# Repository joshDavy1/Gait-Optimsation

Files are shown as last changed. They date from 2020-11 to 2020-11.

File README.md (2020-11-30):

# Generation of Robot Gaits Using Low Level Parameters

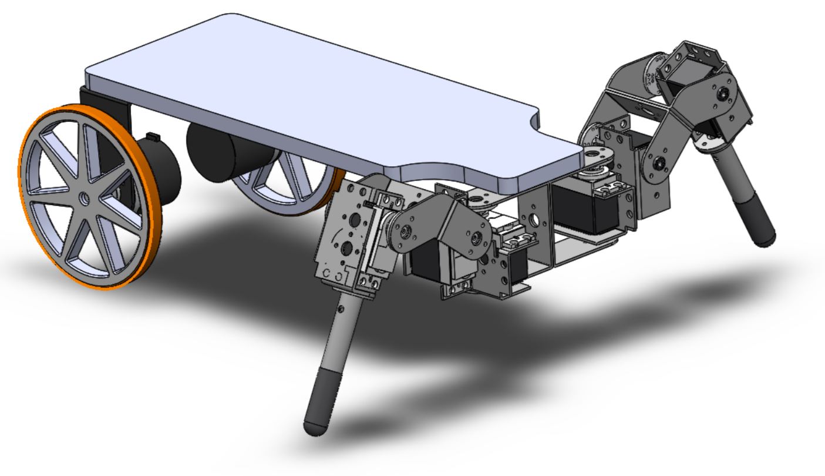
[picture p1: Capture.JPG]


Final Report

Joshua Davy

el17jd@leeds.ac.uk

May 2020

## Abstract

Traditionally the gaits of legged robots are inspired by what is seen in nature and
on assumptions of what properties the optimum gait would have. This involves
kinematic and dynamic analysis of the robot which becomes increasingly difficult
with robots with greater degrees of freedom. Further, real actuators and joints
are not ideal and are also difficult to mathematically model accurately. In this
project the aim is to use optimisation techniques to allow a robot to develop its
own gait free from human bias of what the optimum gait would look like. This
technique means no kinematic or dynamic analysis of a robot is necessary, as
the robot will attempt to learn a policy of moving its joints to optimise its gait.
The project will consist of two main sections, firstly the design and build of
a suitable robotic platform for experimentation and secondly, the investigation
and design of suitable software to control the robotic platform.

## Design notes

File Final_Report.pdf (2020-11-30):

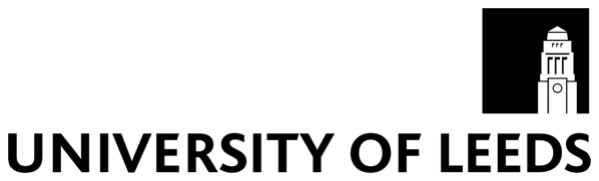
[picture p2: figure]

ELEC3875 Individual Engineering Project 2019-20

## School of Electronic and Electrical Engineering

FACULTY OF ENGINEERING

## ELEC3875

# Project Report

Generation of Robot Gaits using Low Level Parameters

Joshua Davy

SID: 2011483789 | Project No. 33
Supervisor: Dr Craig A. Evans | Assessor: Roger Berry

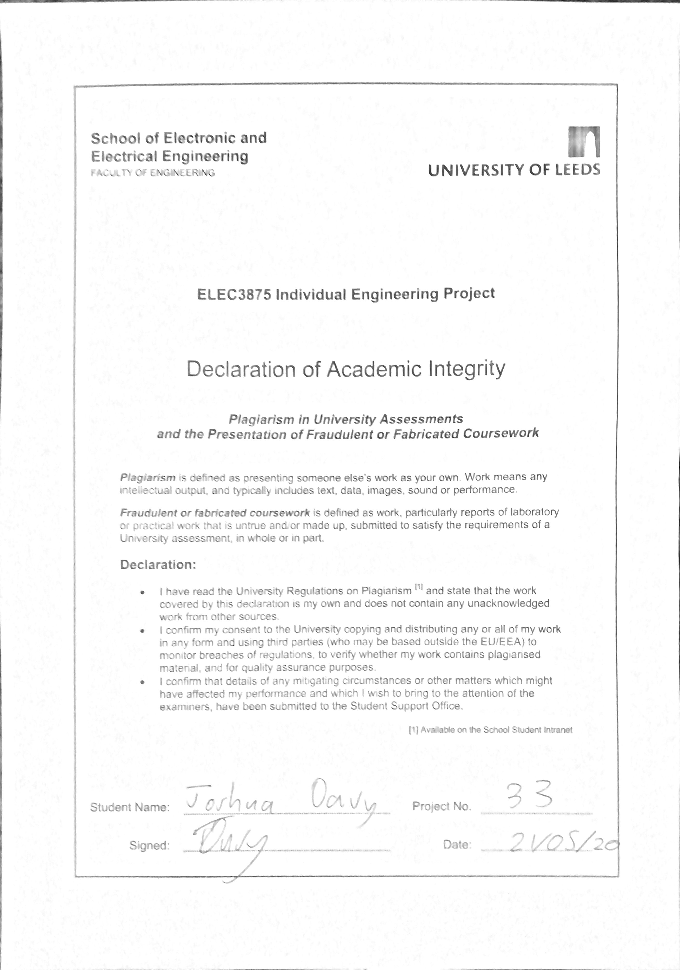
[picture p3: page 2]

# Generation of Robot Gaits Using Low Level

# Parameters

Final Report

Joshua Davy

el17jd@leeds.ac.uk

May 2020

## 1 Abstract

Traditionally the gaits of legged robots are inspired by what is seen in nature and

on assumptions of what properties the optimum gait would have. This involves

kinematic and dynamic analysis of the robot which becomes increasingly difficult

with robots with greater degrees of freedom. Further, real actuators and joints

are not ideal and are also difficult to mathematically model accurately. In this

project the aim is to use optimisation techniques to allow a robot to develop its

own gait free from human bias of what the optimum gait would look like. This

technique means no kinematic or dynamic analysis of a robot is necessary, as

the robot will attempt to learn a policy of moving its joints to optimise its gait.

The project will consist of two main sections, firstly the design and build of

a suitable robotic platform for experimentation and secondly, the investigation

and design of suitable software to control the robotic platform.

3

## 2 Acknowledgements

I would like to thank Dr Craig A. Evans for supervising this project. His help

and support have been vital to this project’s success, and his ability to help

debug and overcome countless issues I’ve faced, has saved me many painful

hours. I would also like to thank Andrew Bilbrough for his technical help. Due

to the COVID-19 outbreak, the final stages of this project had to be completed

from my family home. I would therefore like to thank my mum for her tolerance

of having robotic testing in her kitchen, the dog of which, was less understanding.

4

## Contents

1 Abstract | 3
2 Acknowledgements | 4
List of Figures | 7
List of Tables | 7
List of Algorithms | 7
3 Introduction | 8
4 2D Simulation of Gait Optimisation | 13
5 Platform Design and Build | 15
6 Platform Interface Software | 20
7 Gait Parameterisation | 21
8 Gait Optimisation Techniques | 25

5

9 Results | 29
10 Conclusion | 36
11 Future Work | 37
12 References | 38

6

## List of Figures

1 | MIT Mini Cheetah [2] | | 8
2 | The Single Legged Simulated Robot | | 13
3 | Simulation Results | | 15
4 | Final Platform CAD | | 16
5 | Revised PCB Design | | 19
6 | Human joint angles at comfortable (A) and fast (B) walking pace.
[12] | | 23
7 | Experimental Setup for Flat Surface Optimisation | | 29
8 | Comparison of Gait Parameterisations with Hill Climbing Opti-
misation | | 30
9 | Comparison of Gait Parameterisations with Genetic Optimisation 31
10 | Comparison of Gait Parameterisations with Bayesian Optimisation 32

## List of Tables

1 | Summary of Mechanical Components | | 16
2 | Summary of Changes in Revision 1.1.0 of the Robot Control Board. 18
3 | CMDMessenger [11] Commands | | 21

## List of Algorithms

1 | Stochastic Hill Climbing | | 14
2 | Stochastic Hill Climbing with Random Starts | | | 26
3 | Simple Genetic Optimisation | | 26
4 | Bayesian Optimisation | | 27

7

## 3 Introduction

### 3.1 Project Background

The recent work of groups such as Boston Dynamics and MIT is well known

with many videos featuring legged robots such as Atlas [1] and Mini Cheetah

[2] going viral on social media. Although mechanically these robots are very

capable, the crux of the problem lies in the control. Legged robotics need to

quickly react to changes, understand and process their environment, and plan

their movements accordingly.

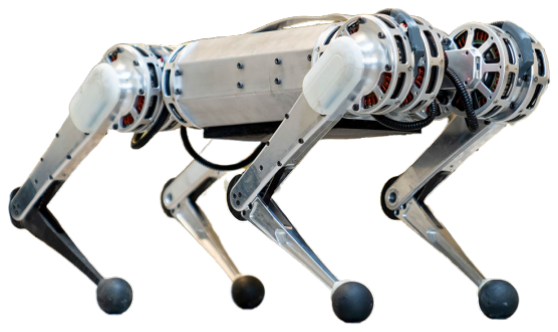
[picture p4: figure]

Figure 1: MIT Mini Cheetah [2]

To this end, often machine learning techniques are applied for the purpose

of robotic control. Learning techniques allow a robot to develop its own control

processes through experimentation with its environment. Machine learning is

the study of algorithms designed to complete an objective without being given

explicit instructions on how to do so. A machine learning algorithm aims to

complete its objective instead by forming patterns found by training [3]. In this

project, the focus is on gait generation for a legged robot. Traditionally the

gaits of legged robots are inspired by what is seen in nature and on assump-

tions of what properties the optimum gait would have. More recently, machine

learning techniques are being applied to the generation of gaits to overcome the

8

issue of designing and optimising a gait by hand. These machine learning tech-

niques require large amounts of test data in order to produce good results and

therefore often rely on simulations where the collection of data is fast and re-

quires no human intervention. The issue of simulations is they require accurate

mathematical models of the robot and its environment which are not always

attainable. In fact, it is impossible for any simulation to perfectly model the

circumstances a robot will face in reality, and a robot whose gait performs well

in simulation may perform poorly in the real world. This issue known as the

reality gap is an active part of robotics research [4]. Several solutions exist such

as Automatic Domain Randomisation [5] or Intelligent Trial and Error (IT&E)

[6].

Of course, these issues could be avoided entirely if instead of simulation, real

robots were used for the evaluation of gaits. This comes with several disad-

vantages. Firstly, the speed it takes to evaluate the gait. In simulation, gait

evaluation can take place as fast as the computer is able to process it allowing

thousands of evaluations in the time it would take a real robot to complete one.

Further, multiple simulations can run in parallel allowing faster evaluation. Al-

though multiple real robots can be used this comes at significant financial cost.

Secondly, in a simulation it may be perfectly reset, whereas in reality this is

impossible meaning no two real gait evaluations will be under the same condi-

tions. Identical gaits tested multiple times may perform drastically differently

in the real world. For these reasons, the optimisation of gaits for state of the

art legged robots rely on simulations for training or a mixture of simulation and

real world testing (Sim-to-Real [7]).

This project considers the problem of gait generation under the following con-

straints:

- No simulation of the robot and it’s environment. All gait evaluations will

need to use the real robot.

9

- No kinematic or dynamic analysis of the robot will be first derived so low

level parameters of the gait will be used. This means, for example, instead

of commanding the position of the foot of the robot, the raw control signals

to the robot motors will be used.

With these constraints the robot platform design is independent from the

gait control meaning the robot’s physical properties or environment could change

and the gait generation process would still be suitable.

As discussed above, these constraints mean the generation of gaits for a mod-

ern dynamic robot in the real world would be infeasible as the training process

would take a impractical amount of time. Therefore, for this project the scope

is limited as follows:

- The used robot platform will be statically stable. This will mean that the

robot is never in a position where another state is unfeasible to move to.

Further, the training process will require less human intervention as the

robot cannot topple.

- The gait control will sensor less and the environment constant (single

state). This means the robot is not expected to make specific plans for

obstacles or path plan. That is not to say that a gait that can deal with

obstacles will not be more advantageous. The gait will therefore be a

constant cyclic pattern, the properties of which will be generated.

### 3.2 Problem Definition

In this approach, the problem of gait generation is framed as an optimisation

problem

π

∗ = argmax

π

f(h(g(π))).

π is the policy, a vector of values that define the current gait. g is the gait

parameterisation; this maps the the policy to the cyclic sequence of control

10 values which form the gait. h is the evaluation function, the testing of a gait

on the real robot. Due to the evaluation taking place on the real robot, h is

slow to evaluate and likely to be noisy due to uncontrollable disturbances. f

is the fitness function. This maps the gait evaluation to a fitness value. The

higher the value of the fitness function will correspond to a better performing

gait. π

∗
is the global maximum. The theoretical policy with the highest fitness

and therefore the best performing policy.

The project has therefore been broken down as follows:

- Firstly, the design and testing of a 2D simulation of a simplified robot as

a initial experiment to test the theory and aim to guide the approach for

the real robot.

- The design and build of a suitable robotic platform complete with elec-

tronics and wireless interface software.

- The design of several gait parameterisation methods. This will allow com-

parison between methods.

- The investigation of suitable optimisation methods.
- The comparison of these optimisation processes with different methods of

gait parameterisations in various scenarios.

In semester one, the focus was on initial design for the robotic platform,

the 2D simulation, sourcing parts, and producing a PCB to host the control

electronics. Due to unexpectedly long lead times on certain key components,

assembly of the platform was pushed to the start of the second semester.

### 3.3 Key Terms

Gait - The pattern of steps a robot makes to walk.

Forward Kinematics - The calculation of the position of the foot of the robot

leg from its joint angles.

11

Inverse Kinematics - The calculation of the joint angles of the robot leg

from a desired foot position.

Parameter - A single parameter describes one property of the robot’s gait.

Policy - The set of parameters that fully describe the robot’s gait. The policy

has a size of n.

Gait Parameterisation - The function that maps the policy to the sequence

of joint positions that form the gait.

Fitness - The resulting score of testing the gait on the real robot. A higher

score corresponds to a better gait.

Parameter Space - The n dimensional space of possible parameter values

mapping to the corresponding fitness. The goal of any of the machine learning

algorithms is to explore this parameter space in search of the maxima.

Local Maxima - A policy in the parameter space which has a higher fitness

then the surrounding points.

Global Maxima - The policy with the highest fitness in the parameter space.

The goal of optimisation is to find this global maxima.

12

## 4 2D Simulation of Gait Optimisation

### 4.1 Simulation Design

A simple 2D simulation of a robot with a singular leg (A crawler robot) was

created in order to test the theory and experiment in simulation.

The code is written in Python and makes use of Pymunk [8] a Python wrapper

for the Chipmunk physics simulation software. The gait was parametrised as

5 sets of pairs of joint angles (for each of the two joints in the leg). The gait

is then formed by cycling through the pairs of joint angles. The policy is then

evaluated by cycling through it on the simulated robot five times and the fitness

is the distance travelled. Optimisation is performed by stochastic hill climbing

where each generation is formed by random variations of the last [9]. Variations

of the policy are formed by varying each parameter with a Gaussian distribution

N (θi
, 0.1) where θi
is the current parameter value. The below link is a video

demonstrating the simulation:

https://youtu.be/vynnbg6c0SE

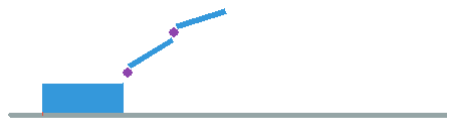
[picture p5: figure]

Figure 2: The Single Legged Simulated Robot

13

Algorithm 1: Stochastic Hill Climbing

currentP olicy ← randomInitialP olicy();

while !done do

polices ← create10RandomV ariations(currentP olicy);

evaluate(polices);

currentP olicy ← getHighestScoring(polices);

end

### 4.2 Results

Results were discussed in depth in the interim report. The main conclusions

of the simulation were despite the simplicity of the optimisation process the

formation of well performing gaits was possible in low number of evaluations.

Due to the inherit randomness of the algorithm, runs could be radically different

in results. With some runs, the algorithm could converge to a policy with a

fitness of over 1000, some runs could not get past 300. This clearly illustrates

the local maxima problem of optimisation where the algorithm gets stuck at a

maxima and cannot improve its policy from there. In Figure 3 we see a typical

run of the simulation. At first the robot makes little progress in forming a gait

until around the 5th generation where there is a radical increase in policy fitness.

After generation 50 the gait no longer makes any meaningful increase in fitness.

This shows the algorithm is stuck at a local maxima as we know better policies

do exist yet the algorithm can longer improve.

14

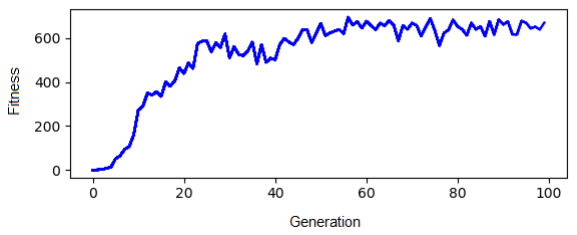
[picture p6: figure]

Figure 3: Simulation Results

## 5 Platform Design and Build

The physical robot needs to be specifically designed in order to suit the gait

training process. Mainly there needs to be a way of accurately measuring ve-

locity feedback from the robot. The system also must be stable in any position

it may find itself in. This is due to the extensive training process the robot will

have to on go to optimise it’s gait. In [9], training was in the order of hours

therefore the robot needs to be able to continue training with minimum human

intervention.

### 5.1 Assembly

The designed platform has two 3-DOF legs at the front with wheels with mounted

encoders at the rear. The purpose of the wheels is to keep the platform stat-

ically stable and prevent the robot toppling. The encoders mounted to the

wheels provide the feedback to the system allowing the measurement of the

robot’s distance travelled, velocity and acceleration. Initially all servos were

Hitec HS-422, however in initial testing the robot did not have the torque to lift

it self off the ground on one leg. The ’knee’ joints of the robot (joint two) were

replaced with high torque Hitec HS-645MG servos to compensate for this issue.

15

A small caster wheel was added to the front of the robot to improve stability

(not shown in CAD). In experimentation the effect of this caster wheel will be

tested.

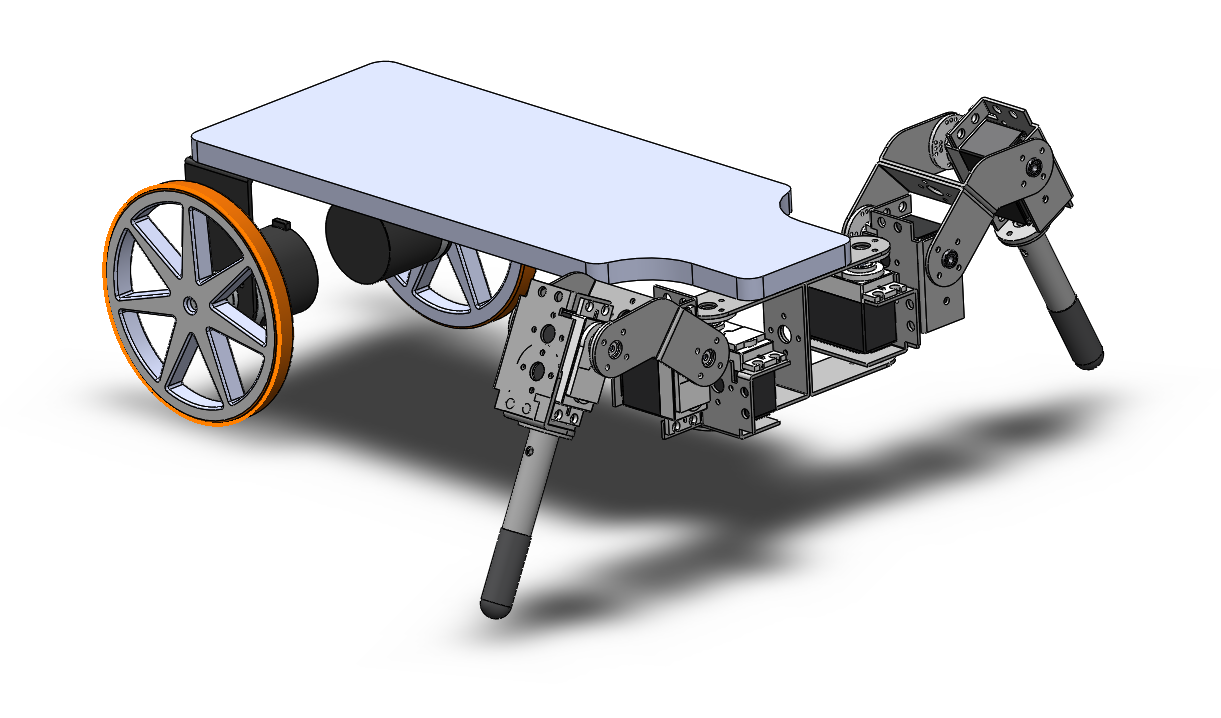
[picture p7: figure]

Figure 4: Final Platform CAD

Component | Description
Lynxmotion 3DOF T-Hex Leg Kit Pair | Robot Legs.
4 x Hitec HS-422 Servos | Servos for joints one and three in each leg.
2 x Hitec HS-645MG | Servos for joint two in each leg.
2 x Aluminum Long ”C” Servo Bracket | Brackets for connecting to robot legs to base.
Robot Base | Laser cut 8mm acrylic robot base.
2 x 400P/R encoders with mount-ing brackets. | Encoders for mounting wheels.
2x 106mm aluminium wheels with rubber coating. | Wheels for rear of the robot. High friction.

Table 1: Summary of Mechanical Components

16

### 5.2 Robot Control Board

For control of the robot a custom PCB was designed to host the main circuitry of

the robot. The board contains a ESP32 [10] microcontroller which was selected

for its WiFi and Bluetooth capabilities, as well as it’s low power consumption

and high processing power. The board contains mounting point for a inertial

measurement unit, a few buttons and LEDs for general use, ten servo mounts

as well as encoder connections. The Robot Control Board was designed to be

a general control board for servo based robot projects. This, along with the

interface software to be open sourced for others to use.

The initial PCB design (Revision 1.0.0) had several small oversights. Once

the design had been fully tested and all issues had been found, a second revision

with several new components and key changes were added (Revision 1.1.0).

Below lists the issues faced with Revision 1.0.0 and the changes made in Revision

1.1.0.

17

Issue | Fix
Servo and encoder pins were mis-labelled on silkscreen. | Silkscreen text was changed to the correct pin names.
Encoder 1 header orientation was opposite to encoder 2. | Encoder 1 header orientation flipped.
Encoder 1B pull up resistor con-nected to Pin 12 of ESP32 causes the processor to fail to boot. | Switched to internal pull up resistors for the encoders.
Pins used for tactile buttons do not have internal pull ups. | External pull up resistors added.
Servos cut out due to lack of cur-rent. | Two 10mF capacitors added to smooth volt-age. Separated microcontroller and servo power rails. Screw terminals added.
IMU used is hard to source and rel-atively expensive. | Switched to a more common and cheaper IMU.

Table 2: Summary of Changes in Revision 1.1.0 of the Robot Control Board.

18

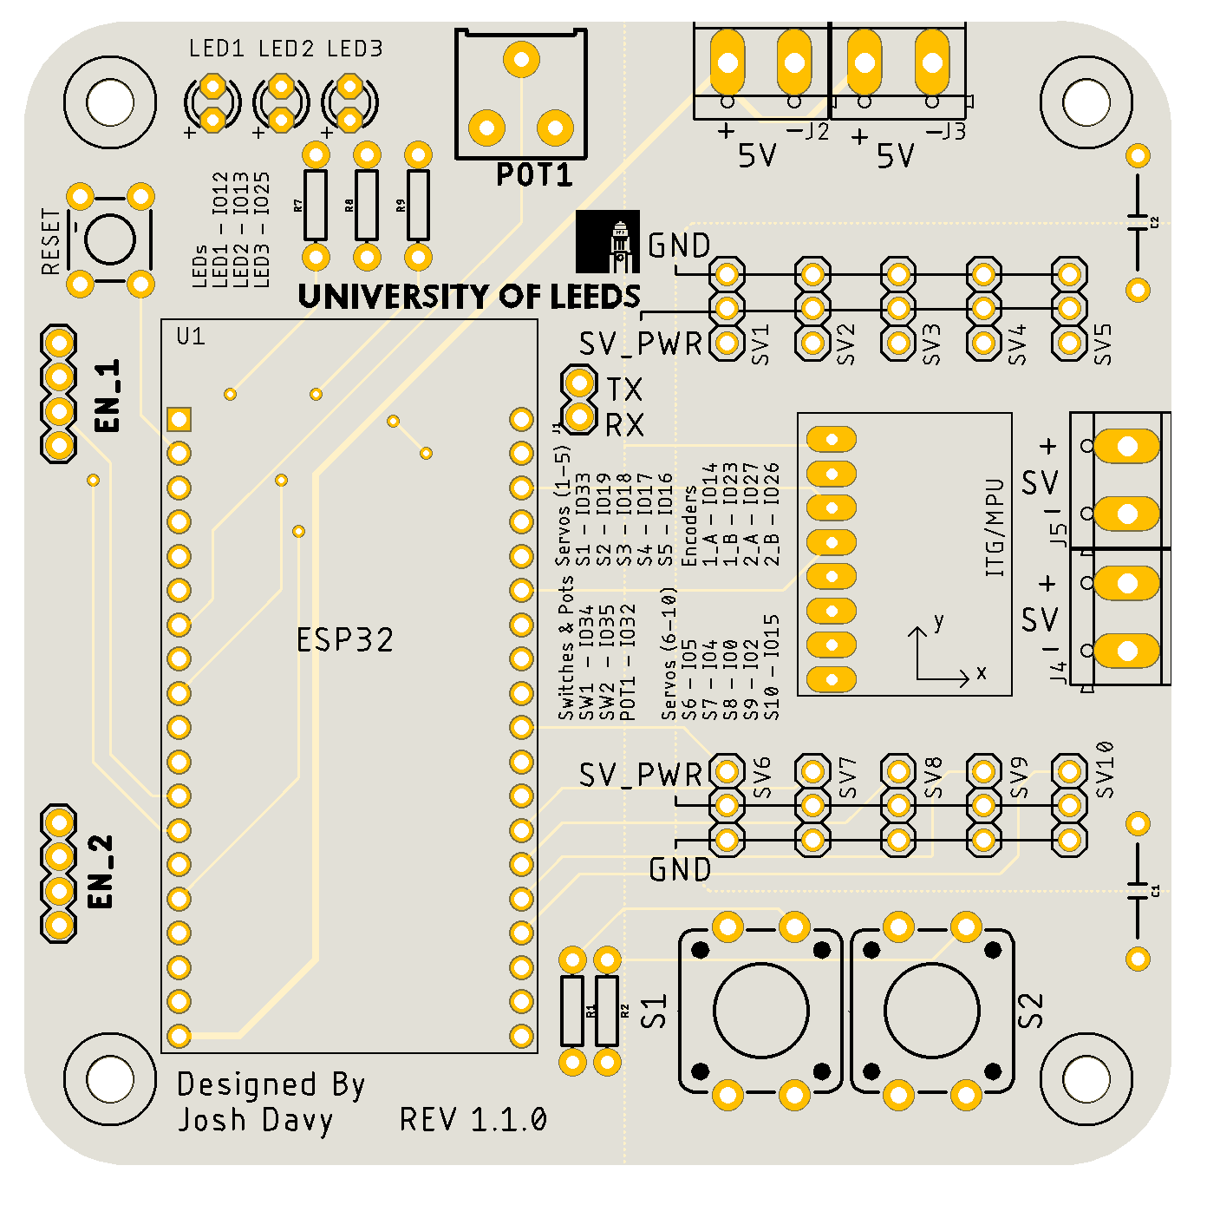
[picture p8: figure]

Figure 5: Revised PCB Design

### 5.3 Power

Originally, the intent was to use a generic 5V 3A rechargeable battery to power

the platform. In initial testing, it was found that this was unsuitable due to not

being able to handle large current spikes caused by the servos. Added parallel

capacitors made little difference. This power loss would cause the Bluetooth

connection between the PC and the robot to be reset and the connection would

have to be reestablished. For the purpose of experimentation, a bench power

supply was instead used to power the robot with a 3 meter cable. With the

second revision of the PCB, the servo and microcontroller power rails were

separated. A separate small USB power bank was then used to power the

microcontroller. This prevents issues caused by voltage drop when the servos

draw large currents. A lithium battery and regulator circuit could be added

if wireless capabilities became necessary however for use in the lab, the bench

19 power supply was adequate.

## 6 Platform Interface Software

For control of the robot, a Bluetooth link between a PC and the ESP32 micro-

controller is used. The ESP32 software processes and executes the instructions

sent by the PC. These instructions are very low level and correspond to, for

example, setting servo angles or reading the encoder values. This way, the ma-

jority of processing can be done on the PC end and will allow fast changes to

the program without having to reprogram the microcontroller. The interface

software communicates using the CMDMessenger serial protocol [11], allowing

for two way wireless communication between the ESP32 and PC. The aim was

to keep this software as well as the PCB as general as possible so they could be

used in other robotic projects without significant change.

The ESP32 has built-in Bluetooth capabilities allowing a wireless serial link

between the host PC and microcontroller. The ESP32 was programmed using

the Arduino framework with the PlatformIO IDE. This was chosen due to the

existence of existing libraries for interface with servos and encoders. The PC

software is written in Python and has accessor functions allowing the control of

the robot’s actuators and reading of the sensors as python data types. In-built

error detection can detect when the established connection has been lost.

20

Command | Parameters | Return Command | Return Pa-rameters | Description
hello | | hello return | | For testing the con-nection.
set servo | servoID (0-9), angle (0-180) | none | | Set servo angle.
set led | ledID (0 to 2), value (0 or 1) | none | | Set LED state.
get button | buttonID (0 -1) | button return | value (0 or 1) | Gets the state of a button
get pot | | pot return | value (0 -255) | Gets button value.
get encoder | encoderID (0 or 1) | encoder return | value | Returns the encoder count.
| | error | | Unexpected command.

Table 3: CMDMessenger [11] Commands

## 7 Gait Parameterisation

In order to optimise, the robot’s gait needs to be represented as a vector, referred

to as a policy. Mathematical optimisation of the gait over the domain will aim

to find the policy which leads to the optimum gait. Two different ways of

representing the gait are compared. Both gaits aim to use low level parameters

as opposed to the solving of inverse kinematics of the robot, and having the

gait parameters as properties of the cyclic shape of the foot’s movement. In the

design of the robot gait parameterisation, a balance has to be struck between

a design which allows as much freedom as possible for the robot to adapt to

it’s environment and keeping the dimensionality of the policy low. Too low a

21 dimensionality would mean the robot’s gait would have limited variations and

there possibly would not exist a suitable gait in the domain for the current

environment. Too high a dimensionality would mean a very large domain, and

due to the time taken for the evaluation of the robot optimisation, it would

struggle to converge on a suitable gait. To help reduce dimensionality of the

gait and speed up training time, each leg will perform the same movement

pattern with the legs moving out of phase with each other. Therefore, the gait

parameterisation only represents the movement of a single leg (three joints).

### 7.1 Linear Interpolated Gait

In this policy the gait is represented as n sets of joint angles. The gait is

formed by cycling through these sets of joint angles with intermediate steps

being linearly interpolated with the full policy π as

π = [[θ1,1, θ2,1θ3,1], ..., [θ1,n, θ2,nθ3,n],

where θj,s is the j

th joint in the s

th step in the gait. n represents the number of

steps in the gait. Possible values of θj,s are limited to the 0 to 180 degree range

of the servo motors.

The policy dimensionality is therefore

d = no.of joints × n,

where in this case, the no. of joints is three. In testing, linearly interpolated

gaits with three and four steps are compared.

### 7.2 Oscillatory Gait

In this policy, inspiration is taken from animal gaits. In animal gaits it can be

observed that each joint moves in a roughly sinusoidal pattern see Figure 6 Each

joint has the same frequency, but the amplitudes and relative phases vary. The

aim is to use this information to parameterise the robot’s gait.

22

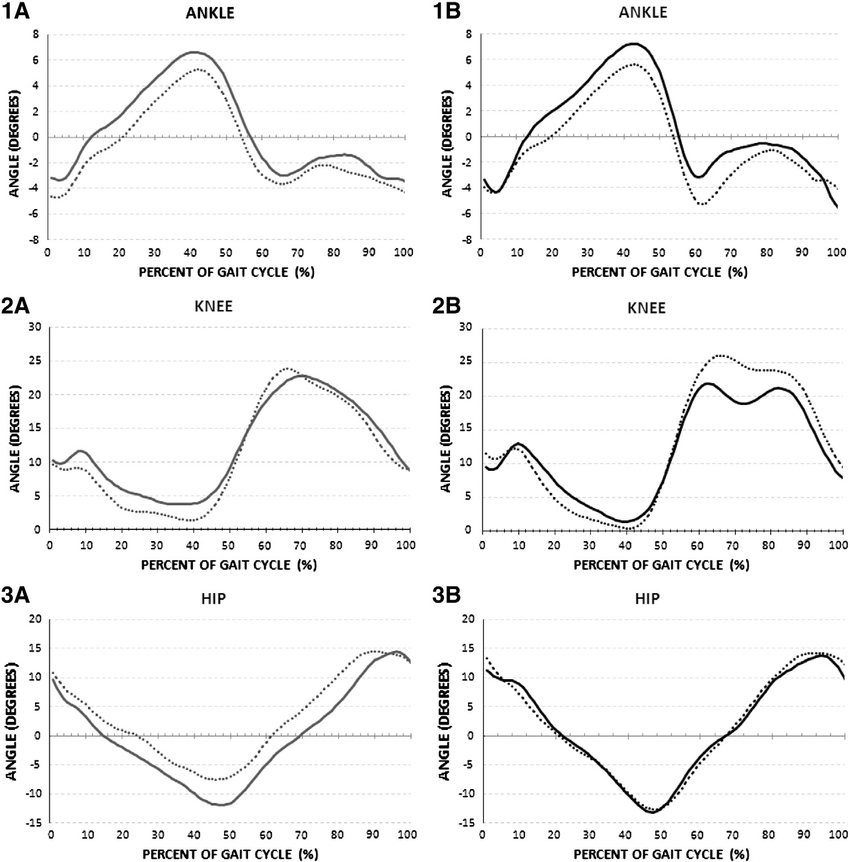
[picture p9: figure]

Figure 6: Human joint angles at comfortable (A) and fast (B) walking pace.

[12]

Therefore each joint is modelled as:

θj,t = Aj sin(ωt + φj )

with the full policy π as:

π = [[A1, φ1], [A2, φ2], [A3, φ3]

where j is the the joint index, t is time, and ω is the fixed angular frequency

(constant for all joints). Aj and φj are the joint parameters. Aj is limited to the

range 0 to 90 to stay within the servo limits. φj is limited to 0 to 180 degrees

23 so joints can be in any phase with any other joint. The dimensionality of the

policy is therefore:

d = no.of joints × 2

### 7.3 Fitness Function

To compare policies they are represented as 200 discrete sets of joint angles to

be sent to the robot. For evaluation, the robot cycles through this sequence

of joint angles with a fixed time step of 0.025 seconds between them, to allow

time for the servos to move between points. The robot runs this sequence three

times and returns the change in encoder measurements which are then used to

calculate fitness. There is a 3 second pause between each gait evaluation to let

the robot settle back to a stable state. During this time the robot lifts its legs

vertically to rest on its wheels. Each evaluation takes 18 seconds.

The testing of a policy returns the difference in encoder values for each wheel

c1, c2 = h(g(π))

where c1 and c2 is the pulse count from the left and right encoder respectively at

the end of the evaluation. This corresponds to the total rotation of each wheel

during the gait evaluation.

To measure the quality of the gait we define the fitness function as follows:

f(c1, c2) = (c1 + c2) − α |c1 − c2|

The fitness function is designed to produce low values for gaits with more de-

sirable traits. The first part (c1 + c2) will produce high values for gaits that

travel the furthest distance. The second part −α |c1 − c2| produces high values

for gait’s that travel in a straight line as it punishes gaits with large differences

between the encoder values. α is a constant. With the 400 pulses per rotation

encoders used a value of 0.05 was used for α. The decision on this value is fairly

arbitrary as it represents the weighting of importance of distance travelled to

how straight the gait is.

24

## 8 Gait Optimisation Techniques

Optimisation will seek to find the optimum policy for the robot. The theoretical

optimum policy is the one that produce the highest fitness. The evaluation of

each gait takes 18 seconds on the real robot. The robot needs to be supervised

and readjusted in between evaluations. This limits the amount of gait evalua-

tions can be made. For the purpose of comparison, each optimisation algorithm

has a maximum of 100 evaluations on the robot. Including adjustment time

this means each optimisation algorithm will have 30 minutes to produce the

best gait possible. Another further challenge is the noise present in the results.

Although efforts are made to make each gait evaluation have the same environ-

ment noise in the results are inevitable. The ideal optimisation algorithm would

make the most out of its limited gait evaluations, be resistant to noise in these

results and produce a policy with the highest fitness possible. For the purpose

of optimisation all policy parameters are scaled to the range [0, 1].

### 8.1 Hill Climbing with Random Starts

As seen in the simulation (Figure 3), hill climbing, despite its simplicity is an

effective optimisation algorithm. The main issue seen in the simulation was the

issue of local minimas leading to different runs of the algorithm producing very

different results. Therefore, the algorithm here is modified to firstly evaluate

five random policies then choose the best one to begin hill climbing with. This

will prevent the algorithm starting with a poor initial policy and lead to a better

chance of reaching a good policy in the limited gait evaluations. Hill climbing,

due to its simplicity and somewhat random approach provides a good bench-

mark to compare more complex optimisation processes.

25

Algorithm 2: Stochastic Hill Climbing with Random Starts

polices ← f iveRandomP olicies();

currentP olicy ← getHighestScoring(polices);

while !done do

s polices ← create10RandomV ariations(currentP olicy);

evaluate(polices);

currentP olicy ← getHighestScoring(polices);

end

### 8.2 Genetic Optimisation

Genetic optimisation is a technique based on natural evolution [13]. Policies ex-

ist in a population that go through crossover and mutation operations in order

to improve the population of policies. A crossover operation aims to replicate

breeding in the population where two parent policies are selected and a child

policy is produced by combining parent parameters. A mutation operation

aims to replicate natural genetic mutation in evolution by randomly adjusting

parameters in policies in the hope that this will improve the policy. This allows

exploration of the parameter space in the search of the global maximum.

Algorithm 3: Simple Genetic Optimisation

population ← tenRandomP olicies();

while !done do

populationF itnesses ← evaluateAll(population);

parent1 ← highestScoring(population, populationF itnesses);

parent2 ←

secondHighestScoring(population, populationF itnesses);

childP olicy ← crossover(parent1, parent2);

population ← replaceW orstP olicyW ith(childP olicy, population);

population ← randomMutations(population);

end

26

In this implementation the population was of 10 policies. Crossover oper-

ations were performed by combing the first p parameters of parent1 and the

last p − 1 of parent2, where p is uniformly selected in p ∈ [0, n], where n is the

policy dimensionality. Mutation is performed on 4 random policies in the popu-

lation per iteration, with half of those parameters being randomly changed with

a Gaussian distribution N(µ = θi

, σ² = 0.3) where θi
is the current parameter

value. Genetic algorithms have the advantage that they will cover more of the

parameter space in search of an optimum policy. The mutation aspect allows

small improvements to the policy and crossover allows policies to be combined

so aspects of each that work well could come together to form a improved policy.

### 8.3 Bayesian Optimisation

Bayesian optimisation is an effective way of optimising gaits on real robots

[14] due to working well with low dimensionality, and expensive optimisation

problems. Hill climbing and genetic algorithms can be thought of as trial and

error approaches which rely on randomness to improve their policy. Bayesian

optimisation is different; instead the optimisation algorithm aims to create a

model that represents the real world results of the robot. The optimisation

algorithm uses its evaluations to improve the quality of this model. This model

is much faster to evaluate then the real robot evaluation f(h(g(π))) allowing

the optimisation process to make fast approximate gait evaluations. Therefore,

allowing the limited real evaluations to be polices which it will believe have

higher fitness.
Algorithm 4: Bayesian Optimisation

model = GaussionP rocessRegression();

while !done do

policy ← acquisitionF unction(model);

policyF itness ← evaluate(policy);

model ← improveModel(policy, policyF itness, model);

end

27

The following notes are adapted from [15] The model is formed by a Gaussian

process p(π). This model aims to replicate f(h(g(π))), the real robot evaluation.

A Gaussian process models noise in the results as a Gaussian distribution

p(π) = m(π) + , ∼ N (0, σ²

)

where m(π) is the mean (the expected) value of p(π) and is noise in the results.

Therefore p is distributed as

p | m ∼ N (m(π), σ²

)

A Gaussian distribution is therefore defined in two parts. Firstly, the mean

function m(π) that returns the mean value of p at π and secondly, k the co-

variance function that returns the covariance between two polices k(π, π⁰
) . In

the multidimensional case, for a data set of policies π the evaluation function is

modelled as

p ∼ N (m(π), K)

where K is the covariance matrix of all policies in π

Kij = k(πi

, πj )

The Gaussian process therefore does not just return the expected value of the

evaluation function given a policy, but the expected mean and variances over a

Gaussian distribution. As more evaluations are completed on the robot, the data

set π can be updated, improving the model. The policy to evaluate is chosen

by the acquisition function. The expected improvement function EI(π) is used

here. The next policy to evaluate is the one where the expected improvement

is the greatest out of the domain of all possible polices.

EI(π) = E[max(0, p(π) − p(ˆπ)]

Π = argmax
π

EI(π)

28 where Π is the next policy to evaluate and ˆπ is the current optimum policy.

The advantage of this optimisation technique is that less gait evaluations

will be needed as the optimisation algorithm can use the model to predict those

which will perform poorly and not evaluate them and focus search on the areas

where the expected fitness is high. Bayesian optimisation is widely used in the

tuning of neural network hyperparameters as these are expensive to evaluate

and have noise in the results. The implementation of Bayesian optimisation

was provided by the Scikit-Learn library [16].

## 9 Results

### 9.1 Flat Surface Optimisation

Initial testing was on a flat smooth surface with no constraints on the robot.

The caster wheel is used for all tests. Comparison is made between the three

presented optimisation techniques and three styles of gait parameterisation.

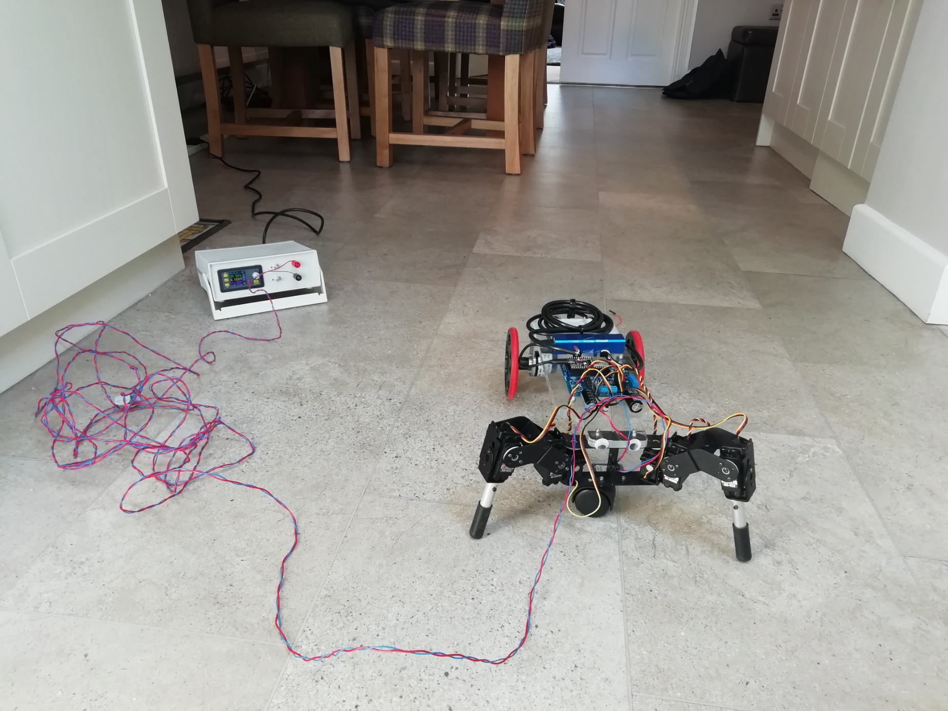
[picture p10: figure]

Figure 7: Experimental Setup for Flat Surface Optimisation

29

### 9.1.1 Hill Climbing with Random Starts

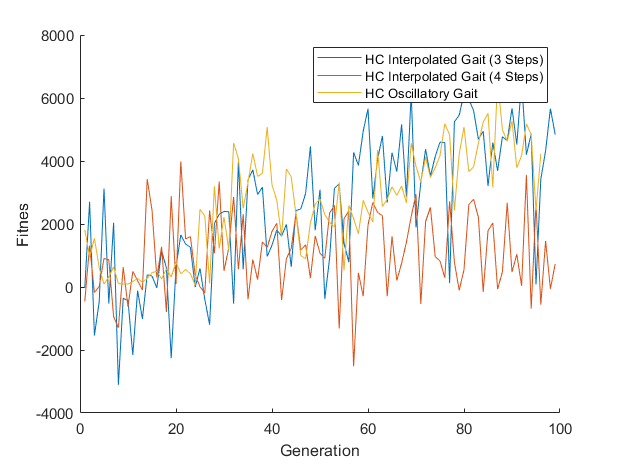
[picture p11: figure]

Figure 8: Comparison of Gait Parameterisations with Hill Climbing Optimisa-

tion

Hill climbing performed well at gait optimisation with three step interpolated

and oscillatory gaits, producing gaits that travelled a good distance (around

1.5m per evaluation) and moved smoothly and sensibly in a straight line. The

five random starts allowed the hill climbing process to start with a good policy

and help converge. However, hill climbing struggled with the higher dimensional

interpolated 4 steps gait. The initial five random starts did not produce a good

starting point policy for the robot and therefore the optimisation process strug-

gled to converge to a good policy as seen in the low end fitness. Despite hill

climbing’s simplicity it does perform well however, is not as robust as other op-

timisation processes due to its reliant on randomness. Despite this, hill climbing

performed well in the noisy environment of gait generation and for the lower

dimensional gaits produced good results in a small number of evaluations.

30

### 9.1.2 Genetic Optimisation

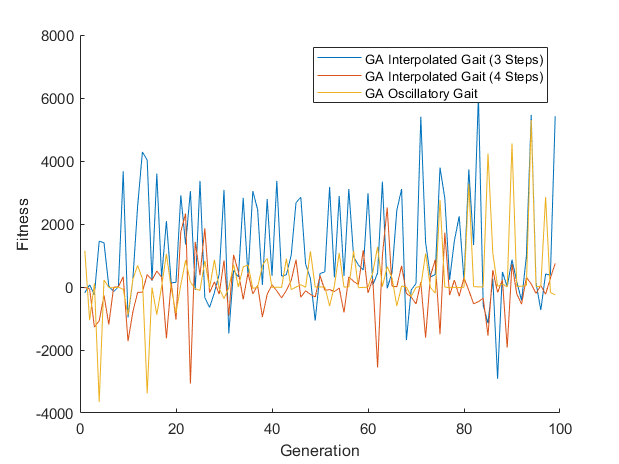
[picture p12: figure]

Figure 9: Comparison of Gait Parameterisations with Genetic Optimisation

Genetic optimisation performed poorly in all cases. With the final population

of polices barely improving from the start point in terms of fitness. Some oc-

casional good policies can be observed but can be attributed to noise and not

the effectiveness of the optimisation process. These policies were not explored

further and reflects the poor performance of the genetic algorithm. This poor

performance was also seen in the work in work of [9]. Genetic optimisation

does not suit well to gait generation. It fails to deal with noise in the read-

ings and converge with the small amount of available evaluations. However,

the volume of the parameter space explored by the algorithm was higher than

the other two optimisation processes and with enough time would have likely of

converged. A further weakness of the genetic algorithm was the crossover oper-

ation. Crossover of policies may make sense in large dimensionality optimisation

problems but here not as much. For example, two polices could perform well

but have leg movements out of phase of each other. Combining these polices

would not produce a better child policy. Genetic algorithms are better suited to

large dimensional, cheap evaluation optimisation problems where there is less

31

noise in results.

### 9.1.3 Bayesian Optimisation

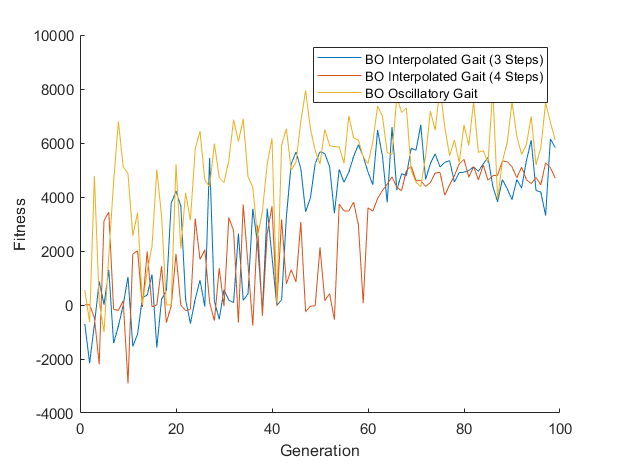
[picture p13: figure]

Figure 10: Comparison of Gait Parameterisations with Bayesian Optimisation

Bayesian optimisation was found to be the most effective of the explored op-

timisation algorithms for gait generation. In this process the highest fitness

gaits were observed. In all gait parameterisations, gaits were observed which

moved smoothly and fast, travelling up to 2m in a single evaluation in the case

of oscillatory gait. Due to Gaussian process regression modelling the noise in

the fitness values, the optimisation process could take that into account when

exploring the parameter space. Looking at the output of the gait generations,

a clear breakthrough point can be observed in all cases. This is where the op-

timisation process has found a policy that performs well and is robust to slight

variations. From then on only small tunings of that policy are needed in order

to improve it as can be seen in the smaller amount of variation after the break-

through. Bayesian optimisation scales well with policy dimensionality, although

it is expected that this would break down as dimensionality increases. The dis-

advantage of Bayesian optimisation is its computational complexity and would

32 be difficult to implement on a simple microcontroller due to the computational

cost of evaluating the Gaussian model. A demonstration of gait generation with

Bayesian optimisation is available here: https://youtu.be/q9s3zgLysts

### 9.1.4 Interpolated Gait

The interpolated gait parameterisation worked well as way of defining a robots

gait. It struck a good balance between allowing a lot of variation in possible

gaits while also converging to a good policy under optimisation. The movement

of the gait could occasionally jolt as the robot moves between steps and was

not as smooth as the sine wave movements of oscillatory gait. The choice of

number of steps depends on how complicated the movements of the robot are

required. With higher steps comes higher dimensionality however and slows

the optimisation process. The dimensionality of the policy is no.of joints ×

no.ofSteps so could scale badly to higher dimensional robots.

### 9.1.5 Oscillatory Gait

Oscillatory gait produced the best performing policy in terms of fitness. Be-

cause all joint movement were based on sinusoidal waves all gaits, even those

that performed badly moved smoothly without jolts. However, this can be a

disadvantage as sometimes jolt movements may be an advantage to a gait. The

policy dimensionality scales well with no. of joints and therefore would be better

suited for higher degrees of freedom robots then the interpolated gait. However,

this comes at the expensive of limitations of the complexity of produced gait as

all joints are locked to sinusoidal movements.

### 9.1.6 Experimental Issues

Some unforeseen issues were observed with the experimental setup. Firstly,

the amount of intervention needed to right the robot if a poor performing gait

caused the robot to topple. This significantly increased the time required to

perform the experiments. In total, it took over 5 hours to test all optimisation

33 process with all gait parameterisations. Secondly, the robot occasionally started

developing undesirable polices that produced a high fitness but were poor gaits.

For example, in the initial run of hill climbing with four interpolated steps, the

robot began to develop polices which involved moving forward then lifting the

wheel off the ground and letting it spin, before performing the same with the

other wheel. This returned a high end fitness as both wheels will have a large

encoder difference from their initial state. When this happened, the run was

restarted.

### 9.2 Optimising with Constrained Movement

### 9.2.1 Without Stabilising Wheel

Testing without the front caster wheel lead to poor results. The hope was the

robot would learn a policy which walked and lifted its front off the ground.

However, the robot would develop a policy which involved dragging its front

across the ground. This is caused by several factors. Firstly, the fitness function

cannot punish policies that involve dragging the robot as it is based on the pure

encoder count. Even if the robot did learn a policy that lifted its front, it

would likely still have a lower fitness than polices that dragged. This could be

solved by using measurements from the IMU to reward polices highly that did

lift the front. However, a more complicated fitness function leads to a more

complicated optimisation surface and would likely increase the required number

of evaluations to form a good policy. Secondly, the process of lifting the front

off the ground would take several steps. This makes the necessary gait complex

as it must combine the lifting and walking.

### 9.2.2 Using Lower Degrees of Freedom

The gait training process was tested with the robot legs locked forward with

the upper joints fixed in position. This constrained the movement of the robot

so a radically different style of gait was needed compared to higher degree of

freedom modes. Similarly to the attempts without the stabilising wheel, the

34 robot struggled to generate a gait in this scenario as it required the robot both

lifting it’s front off the ground and walking forward. The servos struggled to

hold the necessary position against the robots weight.

### 9.2.3 With Only One Leg

Testing with only one leg attached to the robot and the stabilising wheel resulted

in mixed results. For the robot to return a high fitness from a gait there must

be little difference between encoder counts (to encourage the gait to develop to

move in a straight line). This caused issues with generating gaits with one leg

as the robot would move in a curve as the leg pushed against the ground. For

the robot to return a high fitness, the leg would need to move in a very specific

manner in order to keep the encoder difference low. The optimisation process

failed to find a gait capable of this in the low number of evaluations. The gaits

that developed tended to curve away from the side with the leg.

### 9.3 Alternative Terrain Optimisation

Instead of using a flat surface, the gait training process was tested on a more

challenging environment. Grass provided a much more difficult environment

for the robot to train in. Friction is obviously much higher and the terrain

uneven and tall compared to the size of the robot. Bayesian optimisation was

tested with both 3 and 4 step interpolated gaits for the training process, due

to this technique performing well in flat surface testing. With 3 steps, the

robot struggled to form a well performing gait in the environment. The 3 steps

of gait were not enough to form a cyclic pattern of placing the foot moving

it across the ground, lifting and moving forward. With 4 steps a much more

viable gait was formed with the robot moving in a sensible pattern in a straight

line. The servo motors of the robot struggled under the uneven terrain as

more torque was needed to move the robot’s wheels forward compared to the

smooth flat surface. Some of these issues can be observed in this video: https:

//youtu.be/qL6CXBV9FY8

35

## 10 Conclusion

In this project, the process of gait generation for real robots has been explored.

Firstly, a 2D simulation was created which acted as a proof of concept for the

project. In simulation, the hill climbing optimisation algorithm was applied to

a simple model robot to develop a gait and proved the feasibility of the project.

Secondly, a suitable gait training platform was developed. This platform used

commercially available parts allowing quick assembly. A custom PCB was de-

signed to house the microcontroller and support electronics and Bluetooth in-

terface software was developed for communication between the robot and a host

PC. The PCB and communication software was deliberately made very general

in the hope it may be applied to other robotics projects in the future. Several

ways of parameterising the gait of the robot were conceptualised and suitable

optimisation methods were investigated. Finally, gait parameterisations and

optimisation methods were experimented with in various environments to test

their effectiveness and to make comparisons between them.

As seen in the work of [14] and [17], Bayesian optimisation provides a power

tool for gait training. The ability for the process to model the evaluation func-

tion and make predictions on future gaits allow it to effectively form a suitable

gait in the noisy expensive environment. The gait parameterisations presented

provide a strong method for represented robotic gaits at a low level and are not

reliant on the robot kinematics or dynamics to be solved. These methods pro-

vide a good balance between allowing many different gaits available whilst also

keeping the dimensionality low to allow optimisation processes to find quality

gaits in the low number of evaluations available.

Despite this, these techniques have large limitations. Firstly, the time in-

volved to train the gaits cannot compare to the speed of parallelised simulations

which can perform at hundreds of evaluations per minute. Secondly, here the

fitness function has been kept very simple; this simplifies the optimisation sur-

face and helps the robot find a suitable gait more quickly. The issue of this

simple fitness function is that it can return poor gaits with high fitness, as it is

36 difficult to write a simple fitness that can well define all the desired properties

of gait (e.g. stability, speed, smoothness etc...). It was also seen how some gaits

learnt to exploit the fitness function to find adversarial gaits.

## 11 Future Work

Higher dimensional gaits could be explored which would allow more complex

movements. The oscillatory gait could be expanded by having joint movements

defined as a sum of multiple sinusoids. This will allow Fourier approximations

of functions. However, higher dimensional polices would likely increase the

required number of evaluations to converge. A mechanical reset system to allow

gait training to require no human intervention would make higher numbers of

gait evaluations feasible. As seen in testing, the optimum robot gait very much

depends on its environment. It would therefore be useful to have a robot attempt

to adapt its gait as its environment changes. The robot could therefore could

use sensors to develop uncertainty in the effectiveness of the current gait and

adapt according. The robot could also sense the new environment is one its

encountered before and recall a suitable gait.

Most of the optimisation processes discussed here aim to return the policy

with the overall highest fitness. It would be more desirable if the returned policy

was one with a high fitness but also some resistance to variation. This gait would

be more robust. Therefore, the investigation of a optimisation process that aims

to find the most robust highest scoring policy would further research in this field.

These techniques could be applied to situations where simulations are un-

feasible to design or poorly reflect the real world scenario. For example, soft

robotic actuators are difficult to mathematically model due to their lack of

structure and flexibility [18]. This makes the creation of simulated models of

these actuators impossible. Instead, techniques similar to those presented here

could be applied to train a real world robot. With the advent of techniques such

as additive manufacturing, robots can be rapidly prototyped and tested. The

techniques here could be used not only to adapt the gait of the robot, but also

37 to adapt the design of the robot itself. It would have to be seen if results could

be obtained in a low number of evaluations to make this feasible.

Learning to optimise techniques represent optimisation as a reinforcement

learning problem. These learnt optimisers have been shown to outperform

Bayesian optimisation in tasks such as neural network hyperparameter tun-

ing [19]. These learnt optimisers could be applied to gait generation tasks.

It could be investigated how well optimisers trained for other expensive noisy

tasks would apply to gait generation. Further, these optimisers could be trained

with gait generation on a variety of different simulated robots. These could be

compared with optimisers that have been trained on unrelated tasks.

## 12 References

[1] Boston | Dynamics, | Atlas | Robot, | Available | at

https://www.bostondynamics.com/atlas, 2020

[2] Ben Katz, A Low Cost Modular Actuator for Dynamic Robots, Mas-

sachusetts Institute of Technology, 2018

[3] Stuart Russell Peter Norvig, Artificial Intelligence: A Modern Approach,

First Edition, 1995, pp. 5

[4] Jack Collins, Ross Brown, Jurgen Leitner and David Howard. Traversing

the Reality Gap via Simulator Tuning, 2020; arXiv:2003.01369.

[5] OpenAI, Ilge Akkaya et al, Solving Rubik’s Cube with a Robot Hand, 2019;

arXiv:1910.07113.

[6] Antoine Cully, Jeff Clune, Danesh Tarapore and Jean-Baptiste Mouret.
Robots that can adapt like animals, 2014; | arXiv:1407.3501. | DOI:

10.1038/nature14422.

[7] Jie Tan, Tingnan Zhang, Erwin Coumans, Atil Iscen, Yunfei Bai, Danijar

Hafner, Steven Bohez and Vincent Vanhoucke. Sim-to-Real: Learning Agile

Locomotion For Quadruped Robots, 2018; arXiv:1804.10332.

| | 38

[8] Pymunk | Documentation, | Release | 5.6.0, | Available | at

”https://buildmedia.readthedocs.org/media/pdf/pymunk/latest/pymunk.pdf”

[9] Kohl, Nate Stone, Peter, 2004, Machine Learning for Fast Quadrupedal

Locomotion, 78712-1188

[10] Espressif Systems, | ESP32 Datasheet, | Version 3.4, | Available at

https://www.espressif.com/sites/default/files/documentation/esp32 datasheet en.pdf

[11] Thijs | Elenbaas, | CMDMessenger, | 2017, | Available | at

https://github.com/thijse/Arduino-CmdMessenger

[12] Polese JC, Teixeira-Salmela LF, Nascimento LR, Faria CD, Kirkwood RN,

Laurentino GC, Ada L, The effects of walking sticks on gait kinematics and

kinetics with chronic stroke survivors; 10.1016/j.clinbiomech.2011.08.003

[13] Belter, Dominik Skrzypczynski, Piotr, 2010, A biologically inspired ap-

proach to feasible gait learning for a hexapod robot. Applied Mathematics

and Computer Science. 20. 69-84. 10.2478/v10006-010-0005-7.

[14] Daniel Lizotte, Tao Wang, Michael Bowling and Dale Schuurmans , Univ.

Alberta, Automatic Gait Optimization with Gaussian Process Regression,

IJCAI-07-944

[15] Thomas Huijskens, Bayesian optimization with scikit-learn, 2016, Available

at https://thuijskens.github.io/2016/12/29/bayesian-optimisation/

[16] Pedregosa et al, Scikit-learn: Machine Learning in Python, 2011,JMLR 12,

pp. 2825-2830

[17] Calandra, R., Seyfarth, A., Peters, J. et al. Bayesian optimization for

learning gaits under uncertainty. Ann Math Artif Intell 76, 5–23 (2016).

https://doi.org/10.1007/s10472-015-9463-9

[18] Z. Gong, J. Cheng, K. Hu, T. Wang and L. Wen, ”An inverse kine-

matics method of a soft robotic arm with three-dimensional locomotion

39 for underwater manipulation,” 2018 IEEE International Conference on

Soft Robotics (RoboSoft), Livorno, 2018, pp. 516-521, doi: 10.1109/RO-

BOSOFT.2018.8405378.

[19] Bergstra, James; Bardenet, Remi; Bengio, Yoshua; Kegl, Balazs, Algo-

rithms for hyper-parameter optimization, 2011, Advances in Neural Infor-

mation Processing Systems

40

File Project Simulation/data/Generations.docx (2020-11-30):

Generation | | Gait Step 1 | Gait Step 2 | Gait Step 3 | Gait Step 4 | Gait Step 5 | Distance

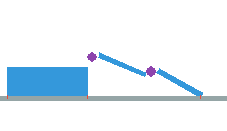
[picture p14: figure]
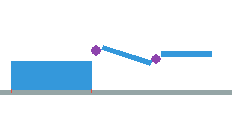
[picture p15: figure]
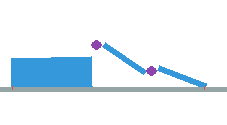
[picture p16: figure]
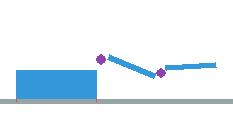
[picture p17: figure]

5 | | | | | | | 61.82

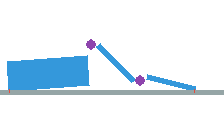
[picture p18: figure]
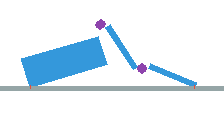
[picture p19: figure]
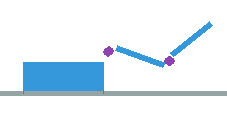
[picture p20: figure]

10 | | | | | | | 226.6

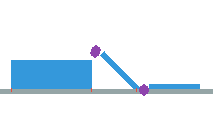
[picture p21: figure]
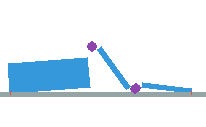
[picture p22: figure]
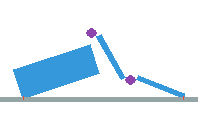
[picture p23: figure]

20 | | | | | | | 448.8

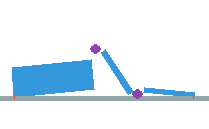
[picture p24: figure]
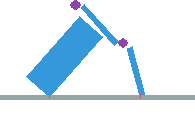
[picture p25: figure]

50 | | | | | | | 641.37


100 | | | | | | | 681.47

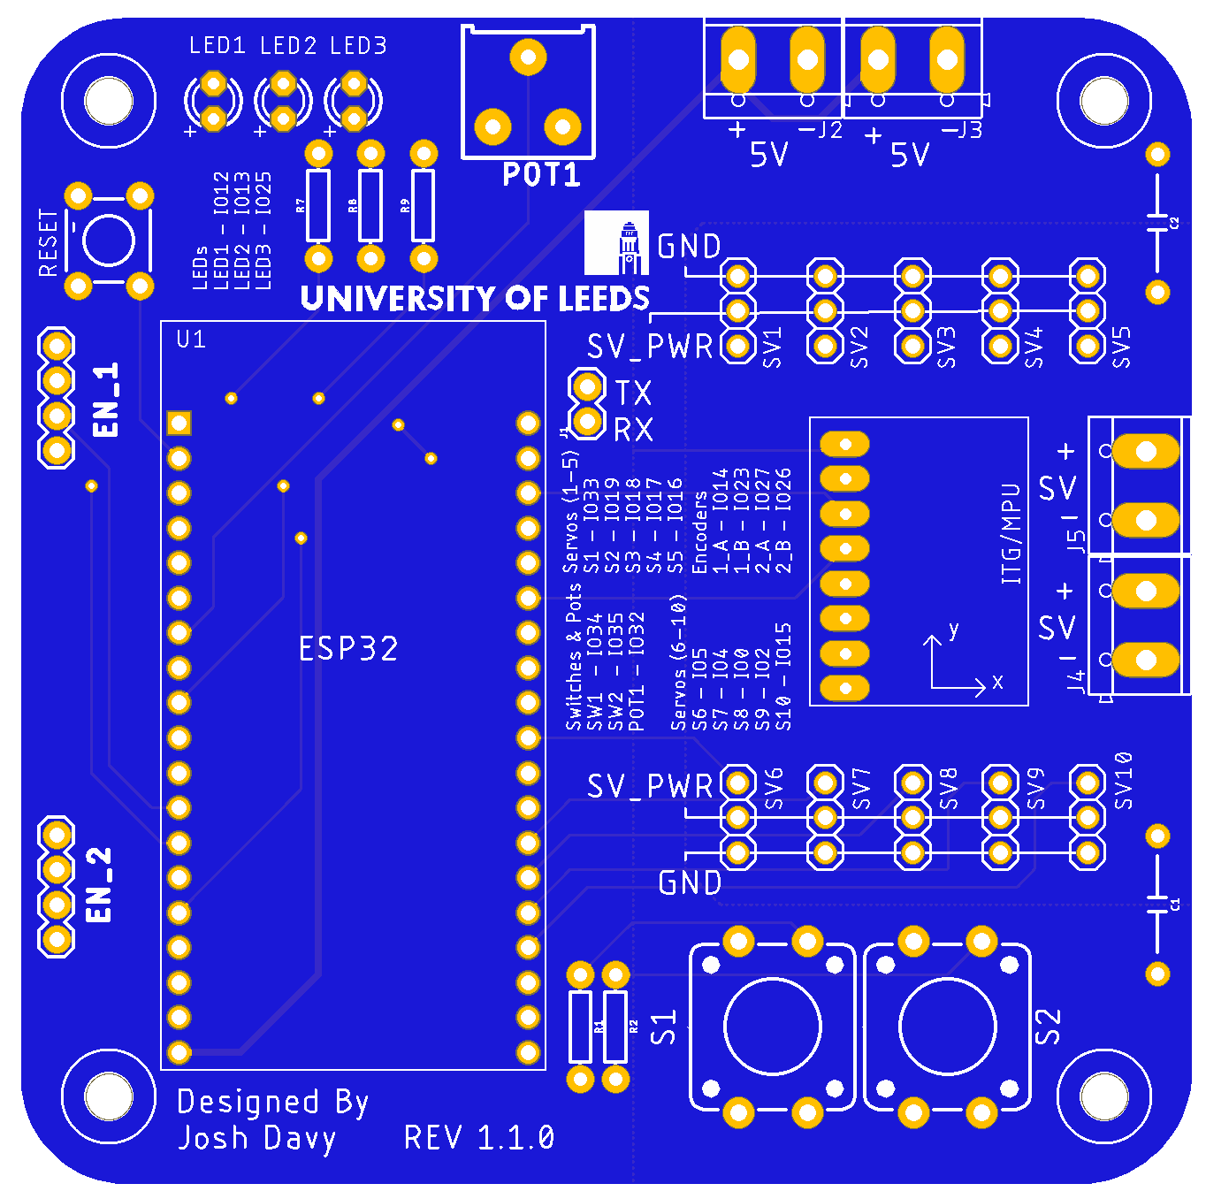
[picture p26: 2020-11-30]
PCB/Robot_PCB/pcb_design.png

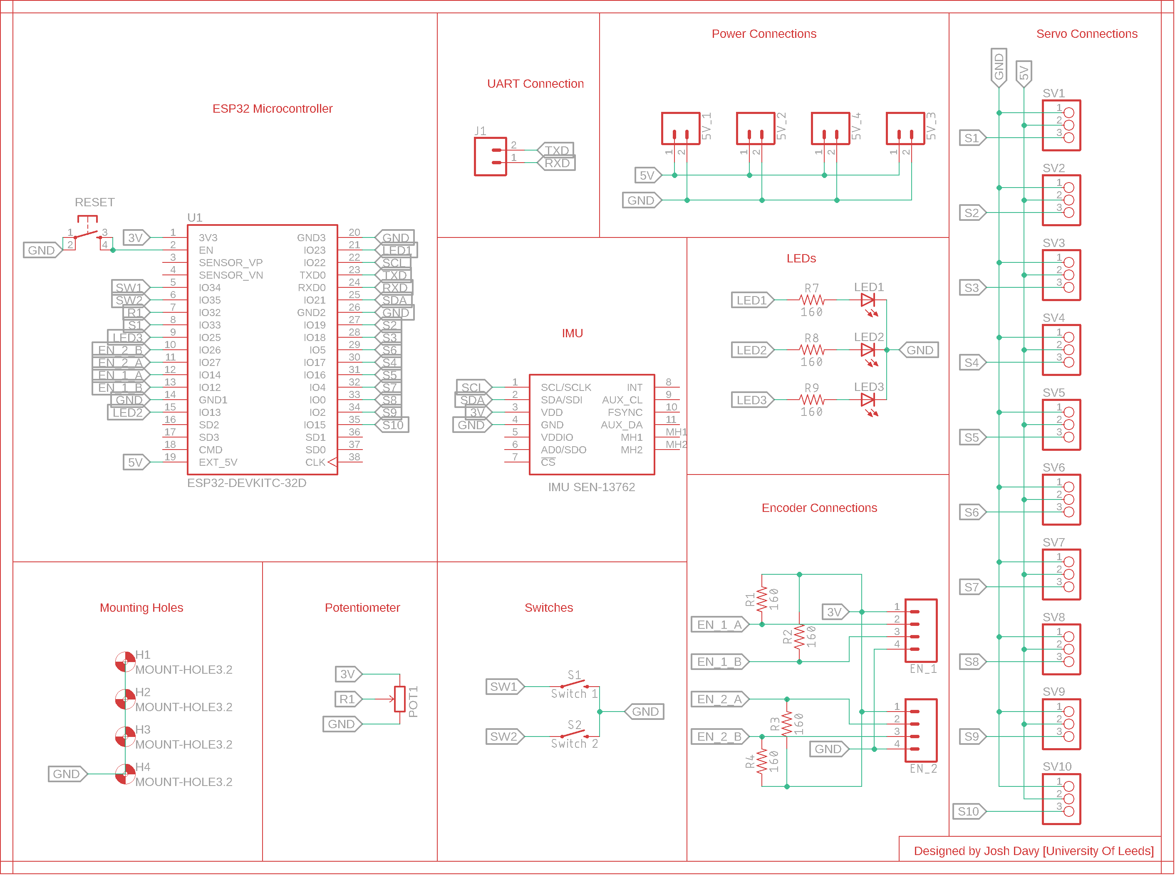
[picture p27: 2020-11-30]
PCB/Robot_PCB/schematic1.png

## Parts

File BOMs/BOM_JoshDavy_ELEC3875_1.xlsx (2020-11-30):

Purchase Order Bill of Materials |  |  |  |  |  | If you are ordering from Onecall/Farnell, please ensure that what you are asking for is not US stock. If a components is, this from will be returned to you.
Name | Josh Davy
Module Code | ELEC3875
Supervisor | Craig Evans
Date Submitted | 2019-11-07
 |  |  |  |  |  | Total: | £162.40
Part Description | Part Number | Quantity | Supplier | Order Code | Price Each | Sub-Total | Notes/Link
18650 | 1 | 4 | OneCall | BT06626 | £8.50 | £34.00 | If u have any lying around let me know and Ill use them instead.
Wheel | 2 | 2 | RobotShop | RB-Prr-14 | £10.24 | £20.48
Encoder + Bracket | 3 | 2 | RobotShop | RB-Dfr-752 | £24.99 | £49.98 | Currently out of stock backorder date is fine
servo hardware | 4 | 3 | RobotShop | RB-Onl-21 | £0.47 | £1.41
ball bearing | 5 | 2 | RobotShop | RB-Lyn-317 | £4.72 | £9.44
fasteners | 6 | 1 | RobotShop | RB-Lyn-84 | £3.76 | £3.76
endcaps | 7 | 1 | RobotShop | RB-Lyn-126 | £1.67 | £1.67
tubing | 8 | 2 | RobotShop | RB-Lyn-113 | £3.56 | £7.12
connector | 9 | 1 | RobotShop | RB-Lyn-111 | £6.62 | £6.62
screws | 10 | 1 | RobotShop | RB-Lyn-245 | £3.34 | £3.34
c connector | 11 | 1 | RobotShop | RB-Lyn-102 | £12.29 | £12.29
offset connector | 12 | 1 | RobotShop | RB-Lyn-103 | £12.29 | £12.29
 |  |  |  |  |  | £0.00
 |  |  |  |  |  | £0.00
 |  |  |  |  |  | £0.00
 |  |  |  |  |  | £0.00
 |  |  |  |  |  | £0.00
 |  |  |  |  |  | £0.00
 |  |  |  |  |  | £0.00
 |  |  |  |  |  | £0.00
 |  |  |  |  |  | £0.00
 |  |  |  |  |  | £0.00
 |  |  |  |  |  | £0.00
 |  |  |  |  |  | £0.00
 |  |  |  |  |  | £0.00
 |  |  |  |  |  | £0.00
 |  |  |  |  |  | £0.00
 |  |  |  |  |  | £0.00
 |  |  |  |  |  | £0.00
 |  |  |  |  |  | £0.00
 |  |  |  |  |  | £0.00
 |  |  |  |  |  | £0.00
 |  |  |  |  |  | £0.00
 |  |  |  |  |  | £0.00
 |  |  |  |  |  | £0.00
 |  |  |  |  |  | £0.00
 |  |  |  |  |  | £0.00
 |  |  |  |  |  | £0.00
 |  |  |  |  |  | £0.00
 |  |  |  |  |  | £0.00
 |  |  |  |  |  | £0.00
 |  |  |  |  |  | £0.00
 |  |  |  |  |  | £0.00
 |  |  |  |  |  | £0.00
 |  |  |  |  |  | £0.00
 |  |  |  |  |  | £0.00
 |  |  |  |  |  | £0.00
 |  |  |  |  |  | £0.00
 |  |  |  |  |  | £0.00
 |  |  |  |  |  | £0.00

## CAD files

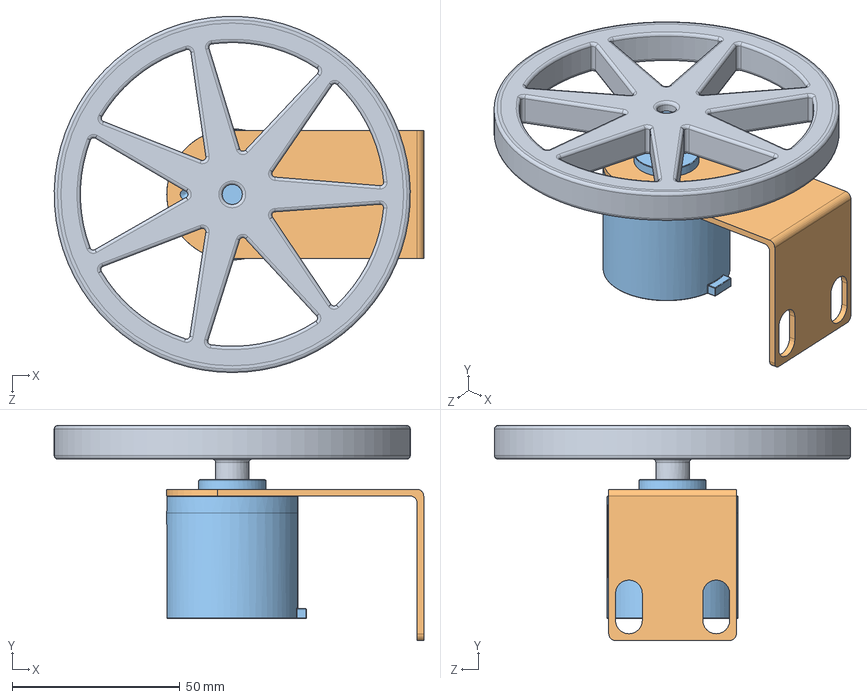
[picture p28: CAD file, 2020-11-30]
CAD/Wheel Assembly/Wheel_Assembly.SLDASM
110.0 x 64.0 x 106.0 mm
106_alum_wheel
encoder_bracket
encoder

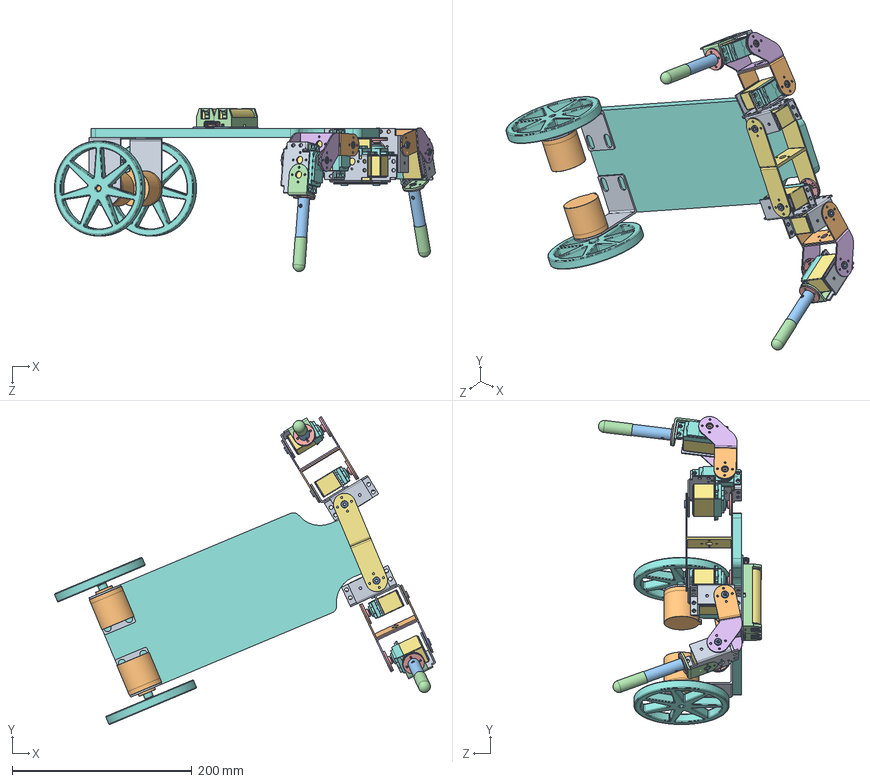
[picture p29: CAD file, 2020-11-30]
CAD/Robot_Assembly.SLDASM
424.2 x 342.9 x 181.6 mm
asb-04 x 6
asb-09 x 2
BB-03 x 6
asb-06 x 2
hub-08 x 2
bottom cover x 6
servo Case x 6
servo cover x 6
spline output x 6
long screw x 24
at-02 x 2
REC-06 x 2
ServoHornPlastic x 6
asb-11 x 2
asb-10 x 2
106_alum_wheel x 2
encoder_bracket x 2
encoder x 2
pcb
18650 Single Cell Holder x 2
femaleThruHoleUSB
Parts - micro_B
Robot_Base

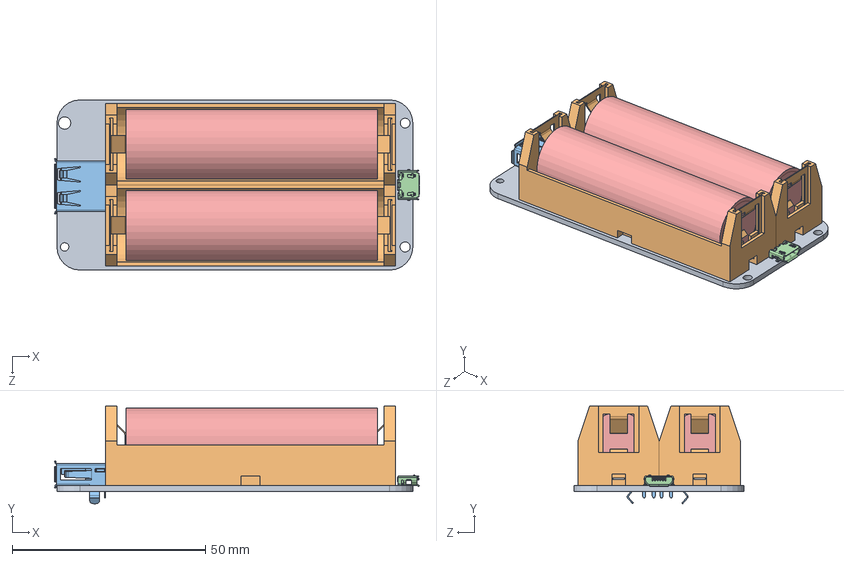
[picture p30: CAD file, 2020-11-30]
CAD/Battery Board/Battery_Board_Assembly.SLDASM
94.3 x 25.2 x 44.0 mm
pcb
18650 Single Cell Holder x 2
femaleThruHoleUSB
Parts - micro_B

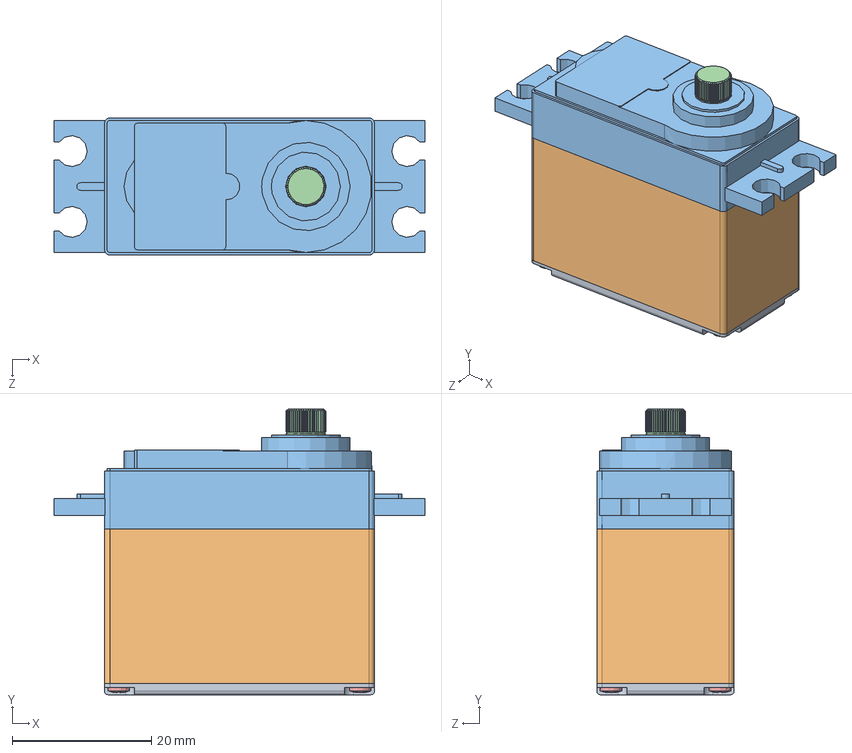
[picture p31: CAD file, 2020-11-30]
CAD/Leg Assembly/servo.sldwks/servo/servo.SLDASM
53.2 x 41.0 x 19.7 mm
bottom cover
servo Case
servo cover
spline output
long screw x 4

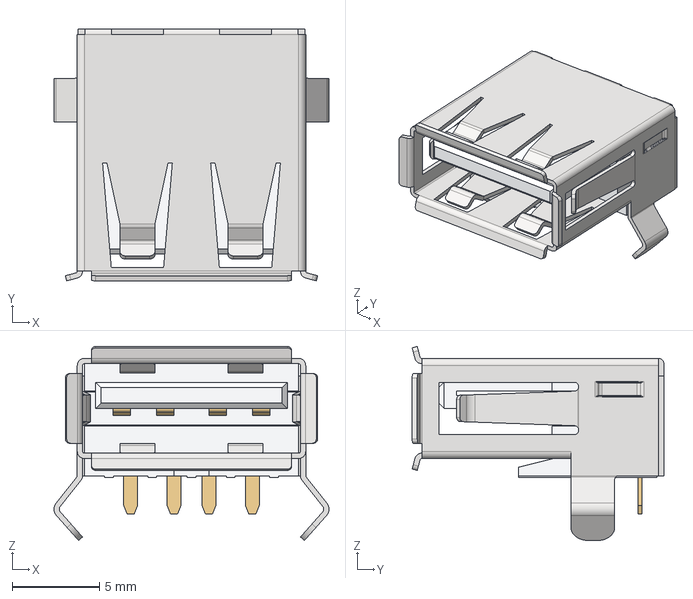
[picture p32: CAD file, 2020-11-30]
CAD/Battery Board/femaleThruHoleUSB.stp
15.8 x 14.4 x 11.1 mm

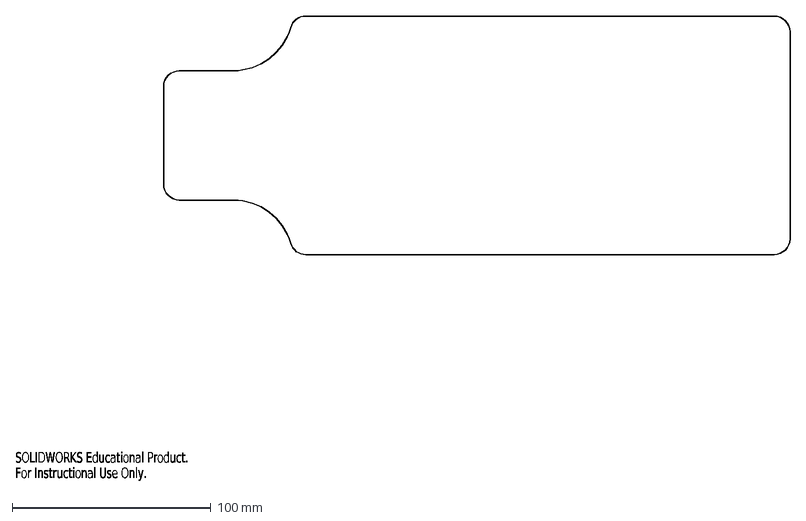
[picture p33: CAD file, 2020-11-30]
CAD/Laser Cutting/Robot_Base.DXF
SOLIDWORKS Educational Product.
For Instructional Use Only.

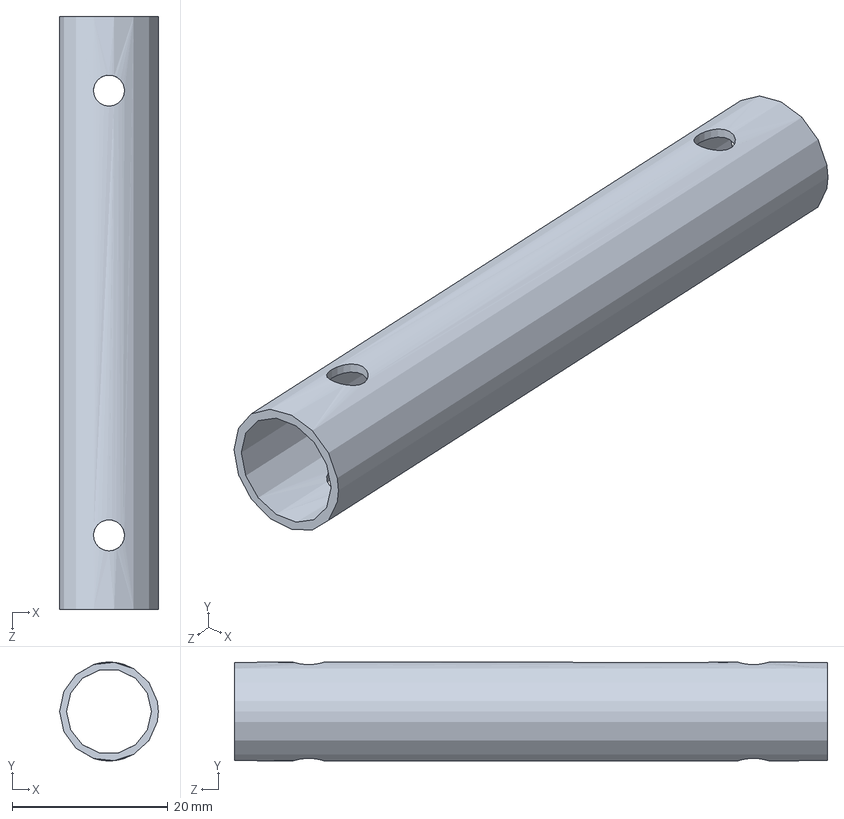
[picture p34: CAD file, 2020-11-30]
CAD/Leg Assembly/at-02.sldprt
12.7 x 12.7 x 76.2 mm

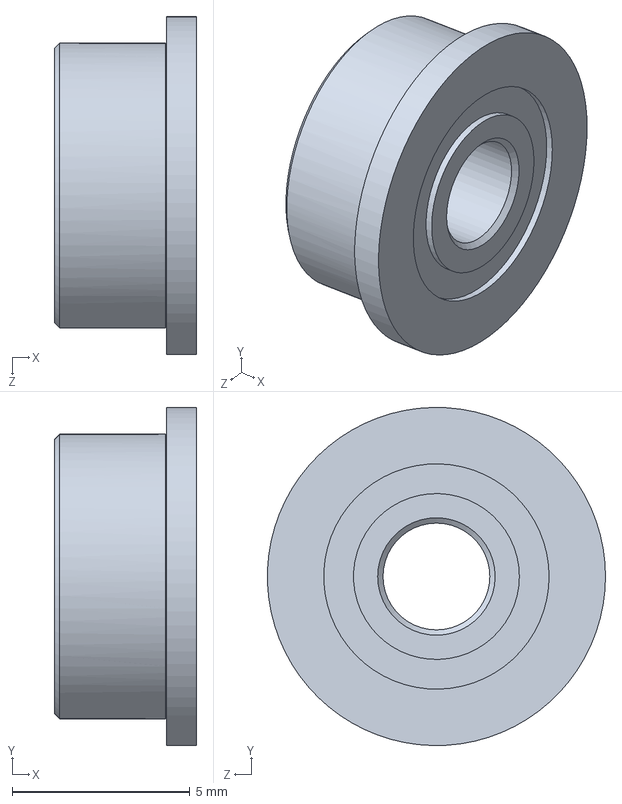
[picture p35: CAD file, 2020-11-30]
CAD/Leg Assembly/bearings.sldwks/BB-03.SLDPRT
4.00 x 9.50 x 9.50 mm

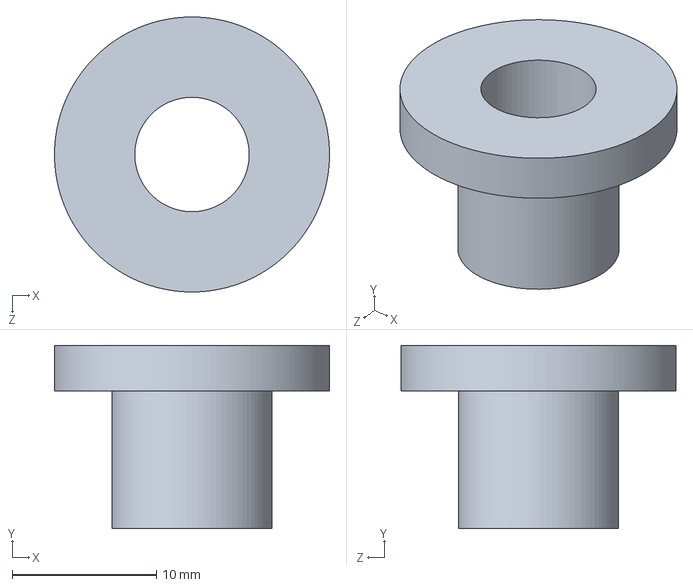
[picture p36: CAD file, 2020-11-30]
CAD/Leg Assembly/recs.sldwks/REC-04.SLDPRT
19.0 x 12.7 x 19.0 mm

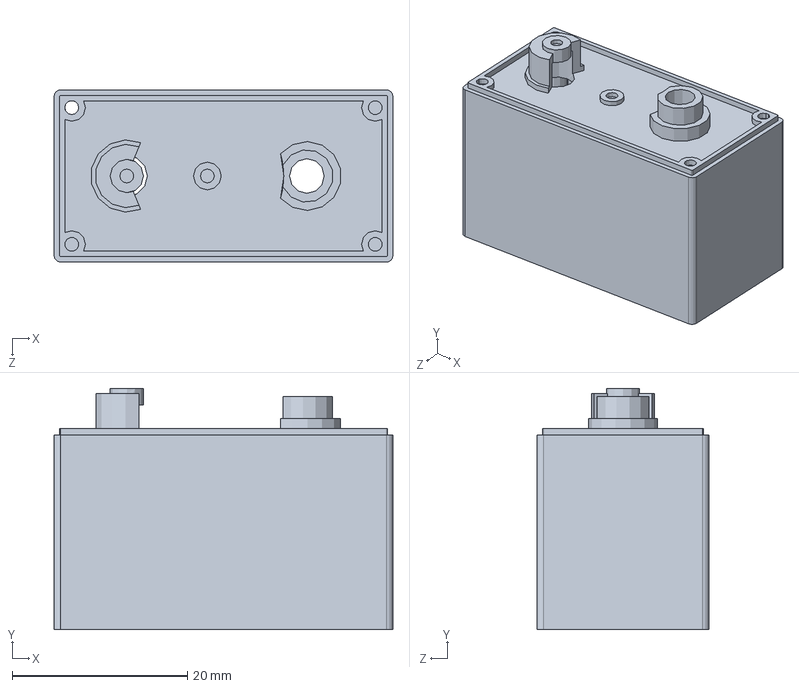
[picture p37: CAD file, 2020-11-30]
CAD/Leg Assembly/servo.sldwks/servo/servo Case.SLDPRT
38.7 x 27.6 x 19.7 mm

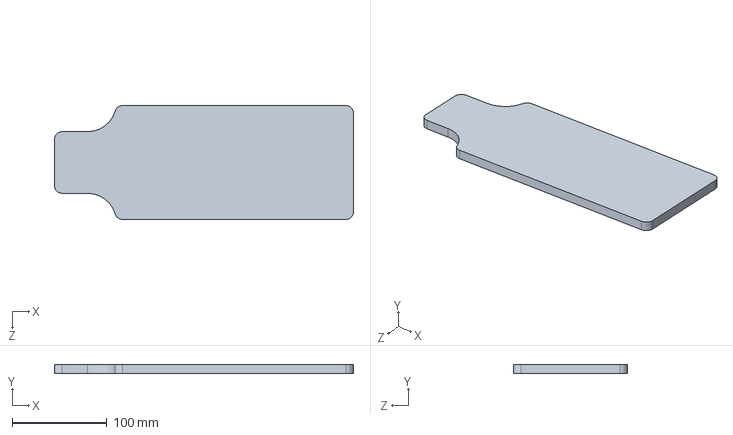
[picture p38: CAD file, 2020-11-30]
CAD/Robot_Base.SLDPRT
315.0 x 10.0 x 120.0 mm

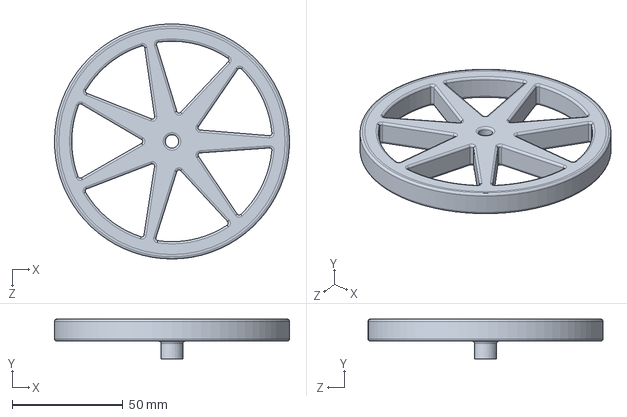
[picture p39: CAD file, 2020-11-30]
CAD/Wheel Assembly/106_alum_wheel.SLDPRT
106.0 x 18.0 x 106.0 mm

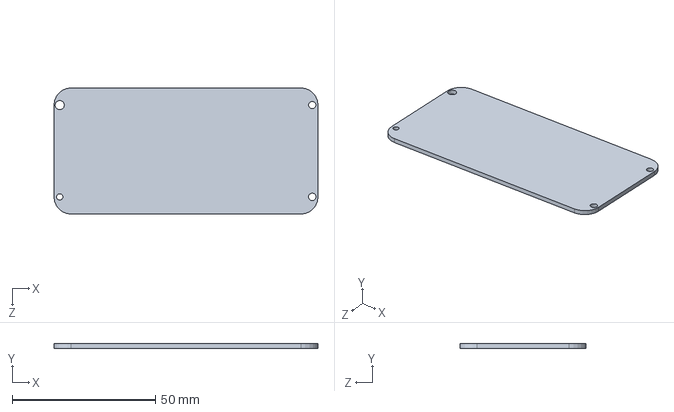
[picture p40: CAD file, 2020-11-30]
CAD/Battery Board/pcb.SLDPRT
92.0 x 1.60 x 44.0 mm

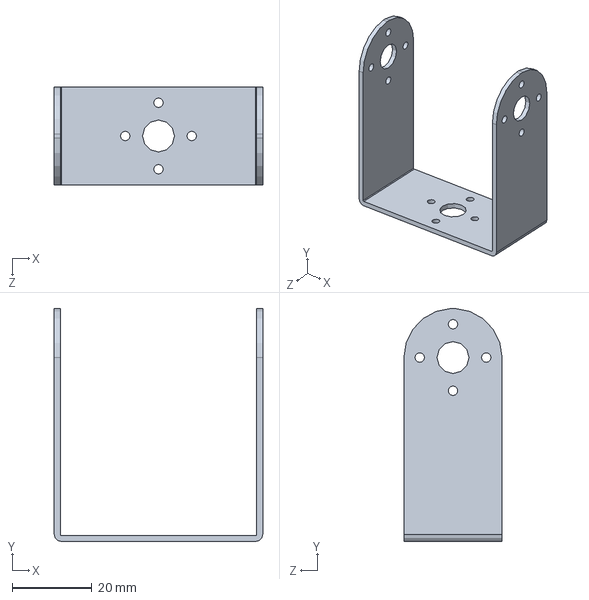
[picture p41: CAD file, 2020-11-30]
CAD/Leg Assembly/asb-10.sldprt
52.2 x 58.3 x 24.6 mm

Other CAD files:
CAD/Leg Assembly/Leg_Assembly_Mirror.SLDASM
CAD/Leg Assembly/bearings.sldwks/BB-02.SLDPRT
CAD/Leg Assembly/recs.sldwks/REC-05.SLDPRT
CAD/Temp_PCB.SLDPRT
CAD/Battery Board/18650 Single Cell Holder.SLDPRT
CAD/Battery Board/18650.SLDPRT
CAD/Battery Board/Parts - micro_B.SLDPRT
CAD/Battery Board/Switch.SLDPRT
CAD/Battery Board/Switch.stp
CAD/Battery Board/femaleThruHoleUSB.SLDPRT
CAD/Leg Assembly/ServoHornPlastic.SLDPRT
CAD/Leg Assembly/asb-04.sldprt
CAD/Leg Assembly/asb-06.sldprt
CAD/Leg Assembly/asb-09.sldprt
CAD/Leg Assembly/asb-11.sldprt
CAD/Leg Assembly/bearings.sldwks/BB-01.SLDPRT
CAD/Leg Assembly/hub-08.sldprt
CAD/Leg Assembly/recs.sldwks/REC-01.SLDPRT
CAD/Leg Assembly/recs.sldwks/REC-02.SLDPRT
CAD/Leg Assembly/recs.sldwks/REC-03.SLDPRT
CAD/Leg Assembly/recs.sldwks/REC-06.SLDPRT
CAD/Leg Assembly/servo.sldwks/servo/bottom cover.SLDPRT
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

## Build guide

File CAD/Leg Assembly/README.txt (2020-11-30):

3x Aluminum Multi-Purpose Servo Bracket Two Pack (ASB-04)
2x Aluminum "C" Servo Bracket with Ball Bearings Two Pack (ASB-09)
1x Aluminum "L" Connector Bracket Two Pack (ASB-06)
1x Aluminum Tubing Connector Hub (pair) (HUB-08)
2x Aluminum Tubing - 3.0" (AT-02)
1x Rubber End Cap Pair - .500" x 1.50" (REC-06)

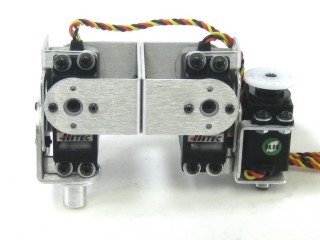
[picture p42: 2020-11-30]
CAD/Leg Assembly/build82b_files/aleg10.jpg

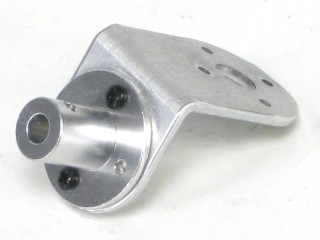
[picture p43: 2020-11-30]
CAD/Leg Assembly/build82b_files/aleg05.jpg

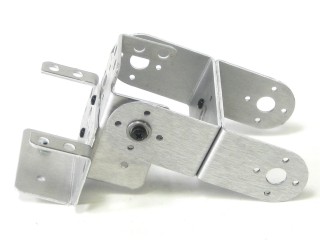
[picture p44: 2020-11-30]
CAD/Leg Assembly/build82b_files/aleg04.jpg

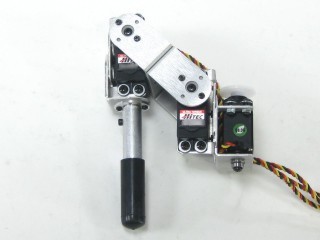
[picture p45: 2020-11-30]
CAD/Leg Assembly/build82b_files/aleg11.jpg

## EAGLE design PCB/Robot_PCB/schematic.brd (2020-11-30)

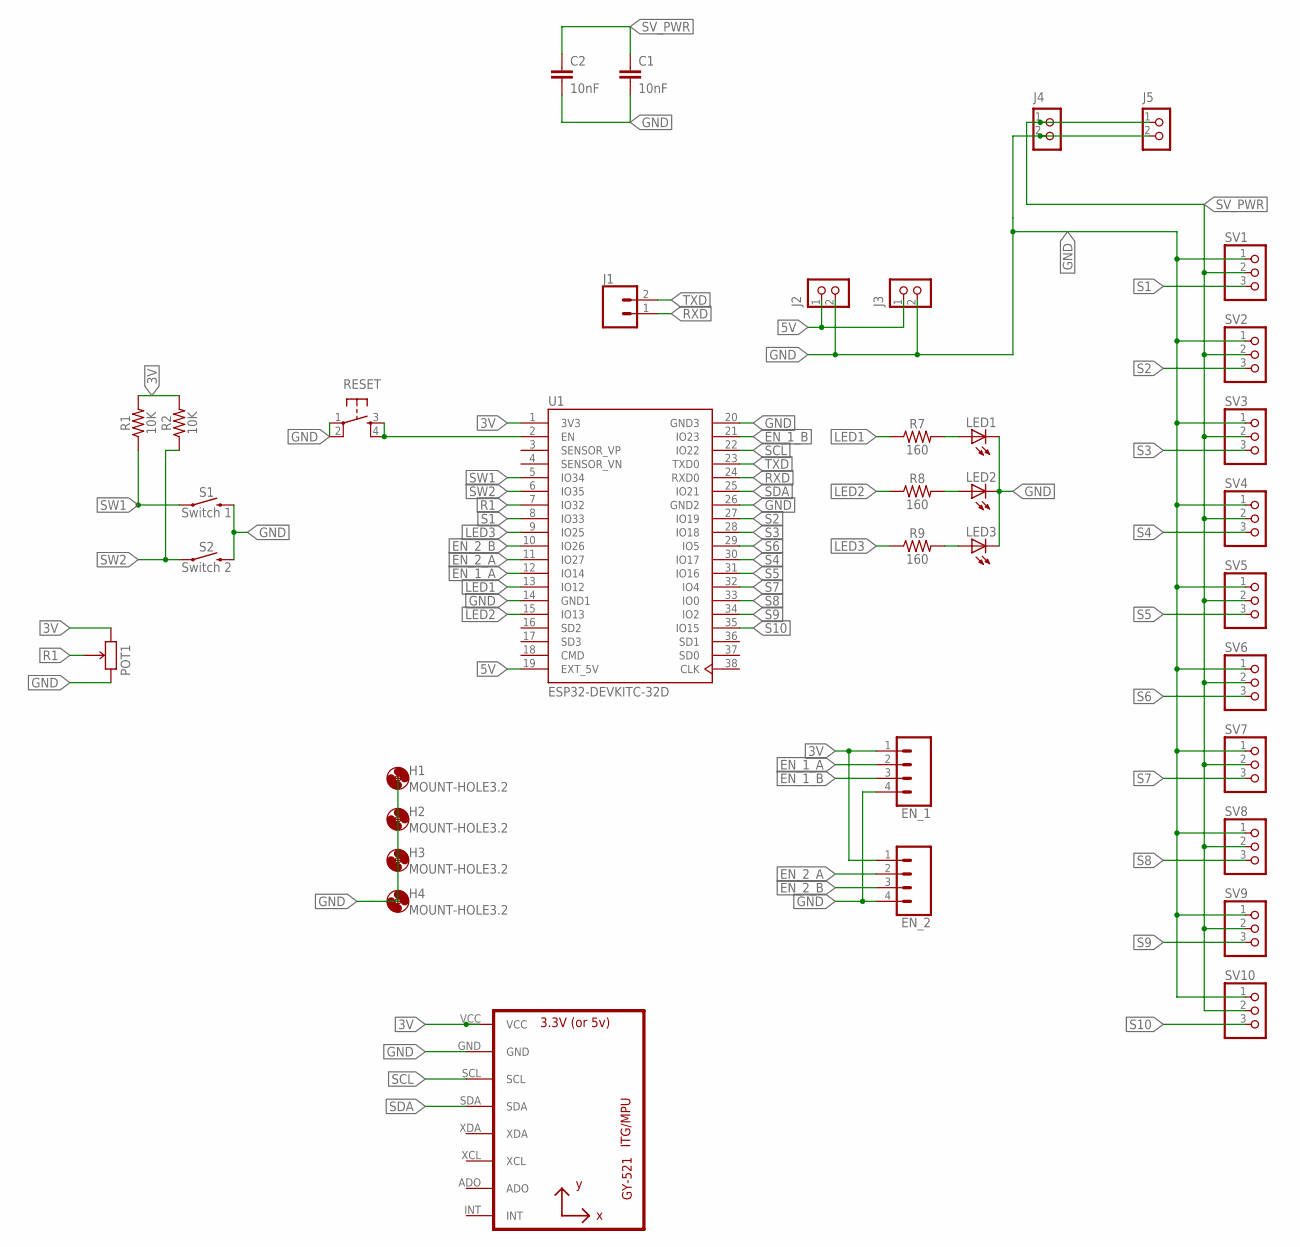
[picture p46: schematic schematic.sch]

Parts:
C1, C2: 10nF; CAP-PTH-10MM
EN_1, EN_2: CONN_04; 1X04
H1, H2, H3, H4: MOUNT-HOLE3.2; 3,2
J1: CONN_02; 1X02
J2, J3, J4, J5: CON_TERMINAL_BLOCK_02-5MM; TERMINAL_BLOCK_2P_5
LED1, LED2, LED3: LED3MM
POT1: POTENTIOMETER_THT; POTENTIOMETER
R1, R2: 10K; AXIAL-0.3
R7, R8, R9: 160; AXIAL-0.3
RESET: TAC_SWITCHPTH; TACTILE-PTH
S1: Switch 1; TACTILE_SWITCH_PTH_12MM
S2: Switch 2; TACTILE_SWITCH_PTH_12MM
SV1, SV2, SV3, SV4, SV5, SV6, SV7, SV8, SV9, SV10: PINHD-1X3; 1X03
U1: ESP32-DEVKITC-32D; MODULE_ESP32-DEVKITC-32D
U2: GY-521MPU6050; GY-521

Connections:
3V: EN_1.1, EN_2.1, POT1.3 (CW), R1.P$2 (2), R2.P$2 (2), U1.1 (3V3), U2.VCC
5V: J2.1, J3.1, U1.19 (EXT_5V)
EN_1_A: EN_1.2, U1.12 (IO14)
EN_1_B: EN_1.3, U1.21 (IO23)
EN_2_A: EN_2.2, U1.11 (IO27)
EN_2_B: EN_2.3, U1.10 (IO26)
GND: C1.2, C2.2, EN_1.4, EN_2.4, J2.2, J3.2, J4.2, J5.2, LED1.K (C), LED2.K (C), LED3.K (C), POT1.1 (CCW), RESET.1, RESET.2, S1.3 (2), S2.3 (2), SV1.1, SV2.1, SV3.1, SV4.1, SV5.1, SV6.1, SV7.1, SV8.1, SV9.1, SV10.1, U1.14 (GND1), U1.20 (GND3), U1.26 (GND2), U2.GND
LED1: R7.P$1 (1), U1.13 (IO12)
LED2: R8.P$1 (1), U1.15 (IO13)
LED3: R9.P$1 (1), U1.9 (IO25)
unnamed: RESET.3, RESET.4, U1.2 (EN)
unnamed: LED1.A, R7.P$2 (2)
unnamed: LED2.A, R8.P$2 (2)
unnamed: LED3.A, R9.P$2 (2)
R1: POT1.2 (WIPER), U1.7 (IO32)
RXD: J1.1, U1.24 (RXD0)
S1: SV1.3, U1.8 (IO33)
S2: SV2.3, U1.27 (IO19)
S3: SV3.3, U1.28 (IO18)
S4: SV4.3, U1.30 (IO17)
S5: SV5.3, U1.31 (IO16)
S6: SV6.3, U1.29 (IO5)
S7: SV7.3, U1.32 (IO4)
S8: SV8.3, U1.33 (IO0)
S9: SV9.3, U1.34 (IO2)
S10: SV10.3, U1.35 (IO15)
SCL: U1.22 (IO22), U2.SCL
SDA: U1.25 (IO21), U2.SDA
SV_PWR: C1.1, C2.1, J4.1, J5.1, SV1.2, SV2.2, SV3.2, SV4.2, SV5.2, SV6.2, SV7.2, SV8.2, SV9.2, SV10.2
SW1: R1.P$1 (1), S1.1, U1.5 (IO34)
SW2: R2.P$1 (1), S2.1, U1.6 (IO35)
TXD: J1.2, U1.23 (TXD0)

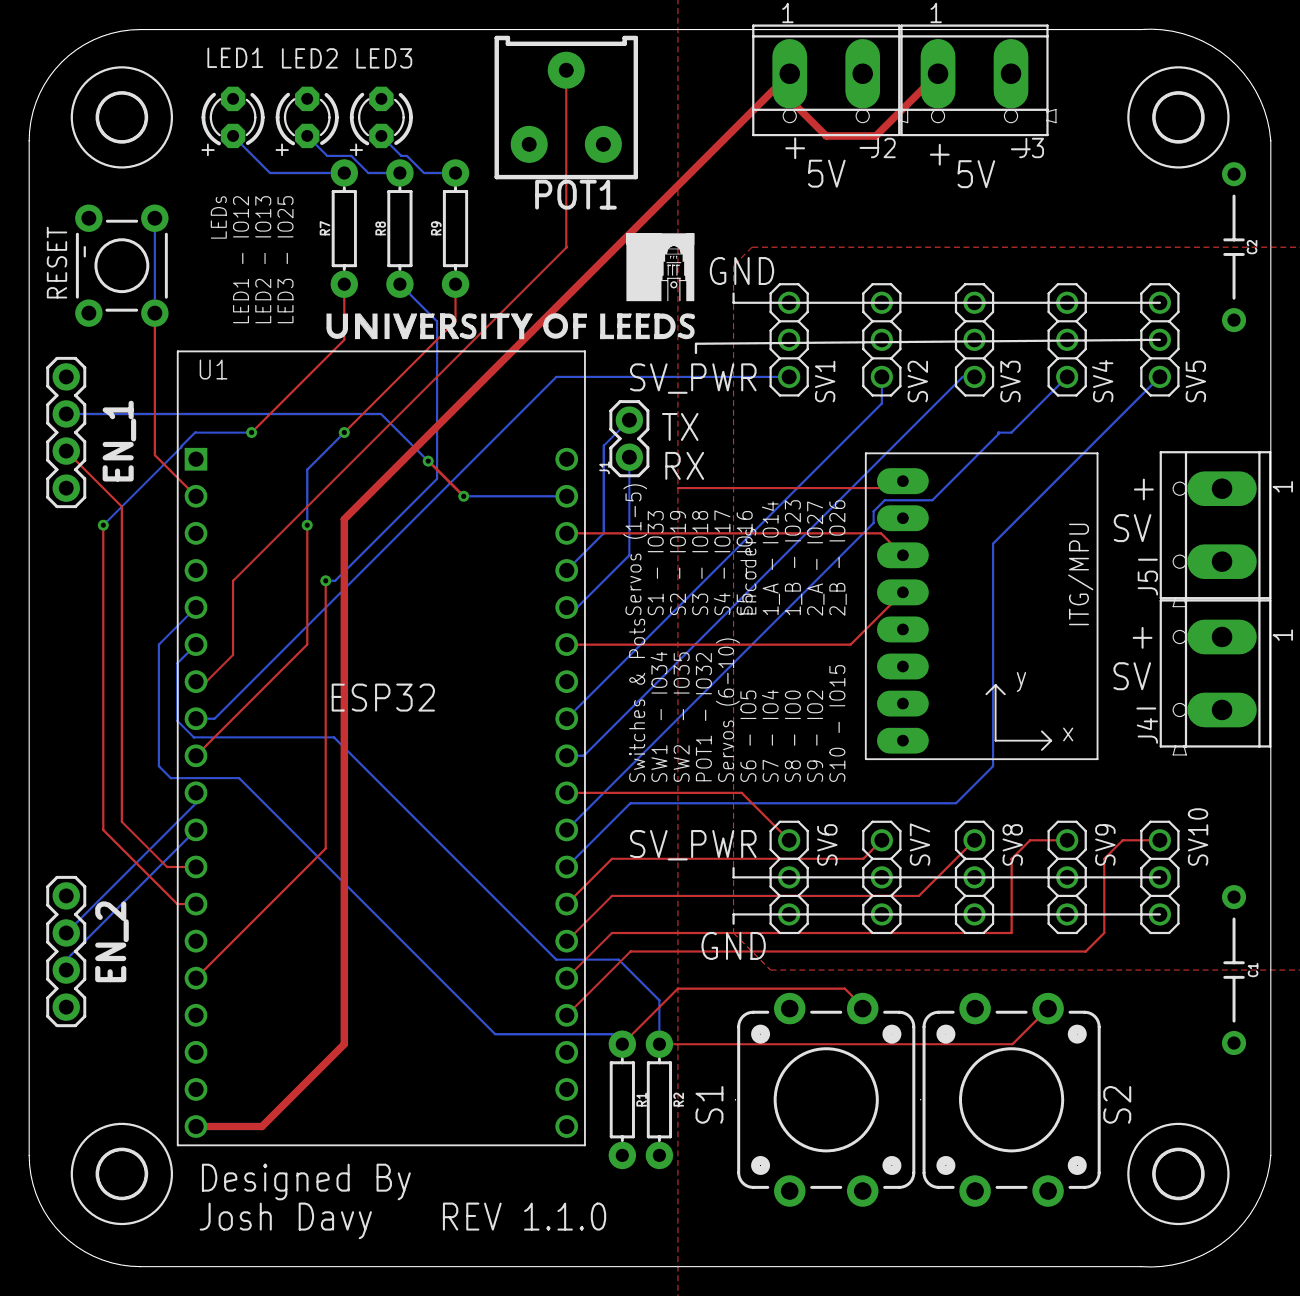
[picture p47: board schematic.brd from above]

Board: 2 copper layers, 85.1 x 84.8 mm, 38 parts (0 on the bottom side), 32 nets.

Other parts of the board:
U$1: LOGO_LARGE

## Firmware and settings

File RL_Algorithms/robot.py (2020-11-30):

## Robot Interface library
import serial
import numpy as np
import PyCmdMessenger
from time import sleep


class Servo() :
    def __init__(self,ID,min = 0,max = 180) :
        self.ID = ID
        self.value = 0
        self.min = min
        self.max = max
        

class Robot() :
    def __init__(self) :
        ## Connect to robot
        arduino = PyCmdMessenger.ArduinoBoard("COM9",baud_rate=9600,int_bytes=4)
        commands = [
            ["hello",""],
            ["hello_return",""],
            ["set_servo","ii"],
            ["set_led","ii"],
            ["get_button","i"],
            ["button_return","i"],
            ["get_pot",""],
            ["pot_return","i"],
            ["get_encoder","i"],
            ["encoder_return","i"],
            ["set_all_servos","iiiiii"],
            ["error",""],
        ]
        self.c = PyCmdMessenger.CmdMessenger(arduino,commands)

        self.servos = []
        for i in range(0,3) :
            self.servos.append(Servo(i,0,180))
        for i in range(3,6) :
            self.servos.append(Servo(i,180,0))

        self.c.send("hello")
        msg = self.c.receive()
        try :
            if msg[0] == "hello_return" :
                print("Hello Message Returned. Sucsessful Connection")
        except :
            "Error: Hello Message Not Returned"

    def setLED(self,ledNo,value) :
        self.c.send("set_led",ledNo,value)

    def setJointRange(self,jointNo,max_servo_value,min_servo_value) :
        i = jointNo
        self.servos[i].max = max_servo_value
        self.servos[i].min = min_servo_value
    def setJointPos(self,jointNo,value) :
        i = jointNo
        self.servos[i].value = value

        pos = self.servos[i].min + (self.servos[i].max-self.servos[i].min)*value
        self.c.send("set_servo",jointNo+1,int(pos))
    
    def setAllJointPos(self,values) :
        for i in range(6) :
            self.setJointPos(i,values[i])

    def getJointPos(self,jointNo) :
        return self.servos[jointNo].value
    
    def recieveMessage(self,expected_message) :
        msg = self.c.receive()
        try :
            if msg[0] == expected_message :
                return msg[1]
            elif msg[0] == "error" :
                return "Error message returned"
            else :
                print("Error: unexpected return message")
        except :
            print(msg)
            print("Error: No message recieved")

    def getEncoderValue(self,encoderNo) :
        self.c.send("get_encoder",encoderNo)
        if encoderNo == 1 :
            return self.recieveMessage("encoder_return")[0]
        if encoderNo == 2 :
            return -self.recieveMessage("encoder_return")[0]
    
    def getButtonValue(self,buttonNo) :
        self.c.send("get_button",buttonNo)
        return self.recieveMessage("button_return")[0]
    
    def getPotValue(self) :
        self.c.send("get_pot")
        return self.recieveMessage("pot_return")[0]

if __name__ == '__main__' :
    robot = Robot()
    x  = 0.5
    robot.setLED(3,1)
    robot.setJointRange(0,0,135)
    robot.setJointRange(3,180,45)
    robot.setJointRange(1,0,135)
    robot.setJointRange(4,180,45)
    while 1:
        x = float(input())
        
        robot.setJointPos(1,x)
        robot.setJointPos(4,x)
        
        #print(robot.getEncoderValue(1),',',robot.getEncoderValue(2))

        # sleep(1)
        # robot.setJointPos(1,0.5)
        # robot.setJointPos(2,0.2)
        # robot.setJointPos(3,0.3)
        # robot.setJointPos(4,1-0.1)
        # robot.setJointPos(5,1-0.3)
        # robot.setJointPos(6,1-0.5)
        sleep(1)
    input()

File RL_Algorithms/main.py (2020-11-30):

import numpy as np 
import random

## Gait Parameter style
from interpolatedGait import InterpolatedGait
from osscilatoryGait import OsscilatoryGait
## Evalute gait on robot 
from evalFunc import evaluation_function
## Minimisation method
from skopt import gp_minimize
from hillclimbing import hillClimbing
from genetic import genetic

# Selected gait method
#method = InterpolatedGait(3,3)
method = OsscilatoryGait(3)
POLICY_LENGTH = method.getPolicyLength()


def main() :
    ## Save policy fitnesses as we go
    filename = input("Enter filename: ")
    def eval(policy) :
        return evaluation_function(policy,filename,method)

    res = gp_minimize(func = eval,
                      dimensions = [[0.,1,] for i in range(POLICY_LENGTH)],
                      acq_func="LCB",
                      n_calls = 50,
                      noise = 500,
                      kappa = 25,
                      verbose = True,
                      n_random_starts = 1,
                      random_state = random.randint(0,999))
    print(res)


if __name__ == "__main__" :
   main()

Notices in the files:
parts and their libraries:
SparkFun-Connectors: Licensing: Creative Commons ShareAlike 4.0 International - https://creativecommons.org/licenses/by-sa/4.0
